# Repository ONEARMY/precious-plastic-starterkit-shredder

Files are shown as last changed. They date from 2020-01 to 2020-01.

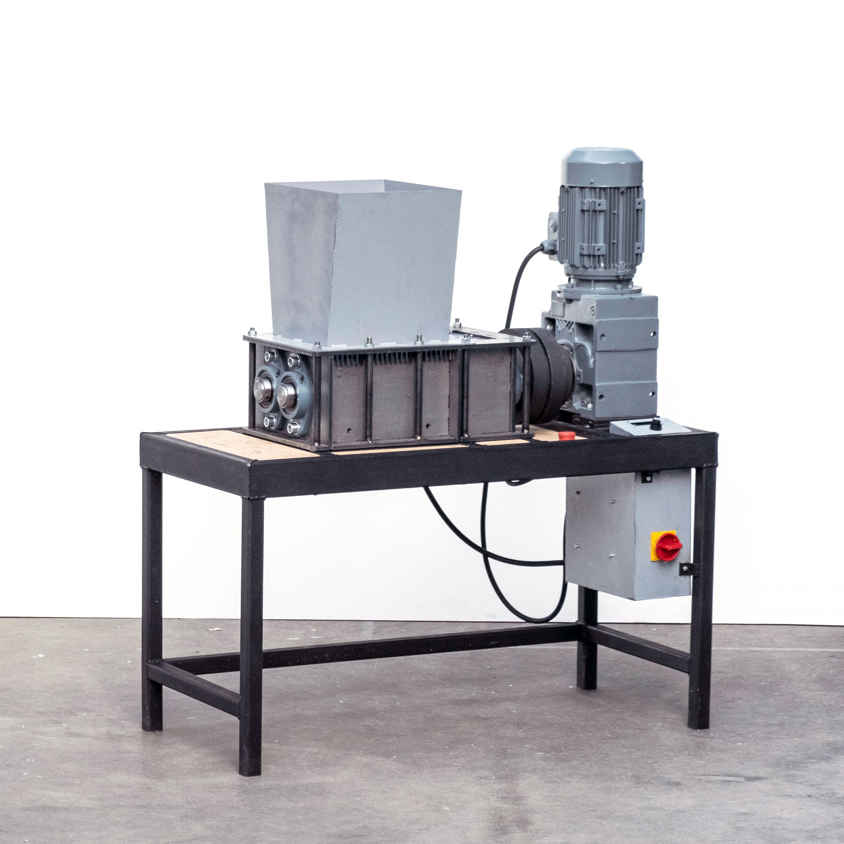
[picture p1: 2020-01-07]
3. Build the machine/Shredder-Pro-image.jpg

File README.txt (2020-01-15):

# Starterkit - Shredder Workspace V1.1

YEAH, you made it into a starter-kit!
Start with the 0. Start folder.. read the introduction text and make sure to watch the videos from our website.

If you have any questions visit our community platform or Discord
https://community.preciousplastic.com/
https://discordapp.com/invite/rnx7m4t

Good luck!!

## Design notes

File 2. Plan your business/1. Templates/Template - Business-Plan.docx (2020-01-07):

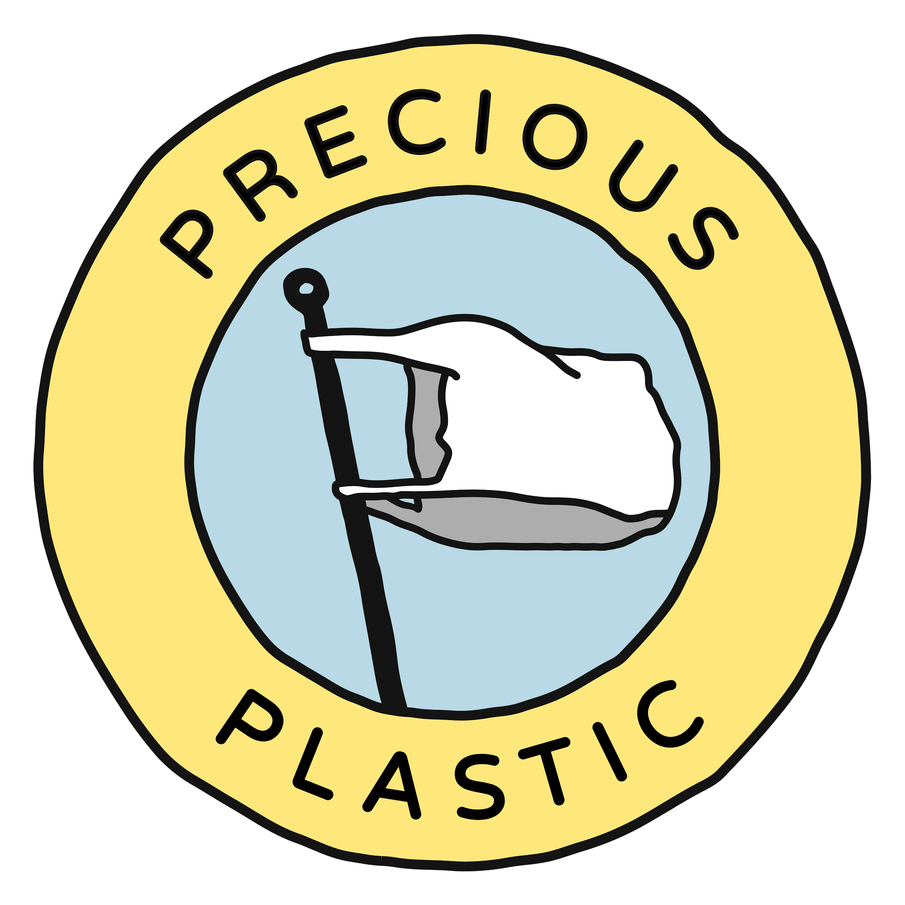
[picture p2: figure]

Your Logo and Business Name Here 👆

# Contact Details

Contact name:

Address:

City:

Zip:

Email:

Phone Number:

Website URL :

# Outline

1. Executive summary
2. Mission
3. Team
4. Market Analysis
  a. Product and Services
  b. Target Groups
  c. Engagement
  d. Sales Channels
5. Operations
  a. Key Resources
  b. Key Activities
  c. Running Costs
  d. Collaborators
6. Impact Measures
  a. Community
  b. Planet
  c. Income Streams
7. Financials
8. Legal Structure
9. Appendix

# 1. Executive Summary

This is your chance to quickly make your argument of what the problem is and how your business is going to solve it. This section shouldn’t be more than a couple paragraphs. Quickly cover the problem, your unique solution, who you’re targeting, and what your impact will be. It’s best to write this section after you’ve completed the whole business plan.

# 2. Mission

What’s the problem?

It’s best to start off describing what problem you’re solving. If your audience might need some education about the plastic waste problem - here’s your chance. What part or aspect of the plastic waste problem are you focusing on? You can set some context about the global plastic waste issue, but make sure to drill down to your national and local level as well. Try to be specific and stress why this is such a big problem facing the planet and your local community. Show your passion for solving this problem. This section will set the stage for the whole story told throughout the plan.

What’s your solution?

Next briefly cover how your solution addresses this problem. For example, if you write about how the plastic waste problem is due to a lifestyle issue, maybe you’re solution is focused on educating people because it addresses the root cause of the problem.

What’s your mission statement?

Look back on your mission that you filled out in the action plan. How can you elaborate to explain it to your reader?

What’s your vision?

Once you have explained your mission - write just a few sentences about your vision. What kind of world do you envision, and what do you envision for your organization?

# 3. Team

Fill in some basic information about your team to show who’s involved and what relevant skills and experience they have to the business.

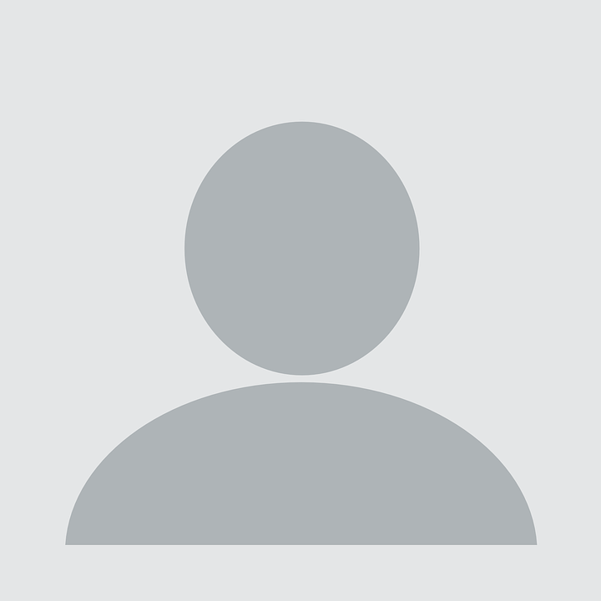
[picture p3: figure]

Name: Role: Experience: | Name: Role: Experience: | Name: Role: Experience:

# 4. Market Analysis

The market analysis section (broken down by the right side of the action plan), is where you will describe how the market is currently performing in your area of interest, how you plan to enter the market, what makes you different, who you are targeting, and how you will deliver your products and services to the customer.

## A. Products & Services

Product explanation

Explain that there is something missing from the market currently and what unique products or services you will offer to meet that unmet need. Write down a brief description of the products and services you are planning to make and include some pictures if possible. Include the price range they will be in and how this compares to similar products/services. If you have any sketches or pictures of your products, you can also include them here.

Product Photos or Sketches:

Competitive advantage

It’s unlikely that your product or service is completely unique - there are businesses or organizations that are probably doing something similar. What are those businesses, what are they offering, and how are you differentiating yourself? Another way to ask this what is your competitive advantage? What are you doing that sets you apart? Describe it here.

Total Available Market

What would you estimate to be the total available market for your product or service? For example, I’m targeting the plastic waste generated in my town, and I know from my city waste department that we generate about 100 tons per month of waste plastic. That means if we were to capture 100 % of the market, we would be processing all 100 tons. If we value each ton at $10, that a $12,000 total available market per year. You should include the total available market that you’re targeting to show how big your business could potentially grow.

## B. Target Groups

Identify the groups

In this section, explain who your target customer groups are, and how many potential customers are in this group. What do you know about these groups? This is your chance to communicate your research about your customers.

Research

What research have you done to show that your target groups will be interested in your products and services? Discuss any field research that you’ve done or online research about these groups. For example, if you’re producing craft furniture from plastic waste, do some research online to see if you can find numbers on the total craft furniture market value in your country. You could also run a small survey in your area to gauge interest in your products.

If you’re targeting businesses, do you have any letters of intent or proof that they are willing to buy your product or service when you’re able to get up and running? This can be a very powerful tool for showing your business case - you already have customers lining up to buy.

## C. Engagement

Engagement is how you will engage with your target customer groups and how many people you can potentially reach with this engagement strategy. What marketing channels are you using? If you’re using social media - which platforms? What’s your engagement rollout plan? Do you intend to start with one marketing channel and then gradually expand? Communicate your marketing plan here.

## D. Sales Channels

Finally, explain what your sales channels are. Explain where and how people can buy your products/services. Explain why you chose these sales channels, and relate that back to your target groups.

Business to Business (B to B) versus Business to Consumer (B to C)

Are you focusing on business to consumer or business to business? This is an important distinction, because it will help the reader understand your business model. Business to consumer (B to C) means that you are targeting consumers directly - you will be the one selling the product or service to the end user. If you are instead focusing on business to business (B to B), that means that you’ll be selling to other businesses. For example - if you’re a machine builder that will be selling machines to new workspaces - this is a business to business model. If you are a product producer selling products directly to people through the Precious Plastic Bazar, this is an example of business to consumer.

# 5. Operations

## A. Key Resources

First explain what key resources, or the key tools, machines, people, and any other resources that are crucial for you to deliver on your mission.

Another good thing to include here is any permits or licenses that you might need from the government in order to be able to operate. Are there any safety requirements that you need to follow? What resources do you need to have available in order to do so? What about people - are there any key skill sets that you need?

Include any pictures of your workspace if it’s relevant as well.

## B. Key Tasks

Explain your key tasks - What actions and activities will you need to focus on? Show that you have a clear sense of what needs to be done. How will produce your product or service and what are the key tasks that you must do to support this core delivery. Describe your production or service delivery process in detail and how you will maintain quality. How do you and your team’s skills and experience match up with these activities?

## C. Running Costs

In this section you will describe in more detail the key running costs that you identified in the Action Plan. Doesn’t need to be very long - this is just to show that you’ve thought about the costs that are a risk to the business month after month. If you have a way to control these costs, discuss that here as well.

## D. Collaborators

Finally, write about who your key collaborators are. What people, groups and organizations will be key in helping you fulfill your mission? Say what they will add to your business, and what your current relationship is with them. Are these people you would like to collaborate with, or you’ve already started? What’s the current status? How will they help you deliver on your mission? Be specific here - show what strategic relationships that you have which will be a strategic asset to your business.

# 6. Impacts

## A. Community

Here’s your chance to write about the positive impact you will have on your community. What’s the direct impact you will have on improving the lives of real people? Link this back to your mission and vision if possible.

You can also discuss your involvement with the Precious Plastic community. Perhaps discuss how you will contribute back to the Precious Plastic open source community and share your knowledge with other Precious Plastic workspaces.

## B. Planet

The planet section is for you to discuss the positive impact you will have on the environment. Show your vision and dream about a cleaner, greener future. It’s important to think about how you will measure this as well. For many Precious Plastic businesses this will be the amount of material recycled.

## C. Income Streams

Next describe your revenue model, or how you intend to bring in money month after month. Refer back to what you wrote in the action plan - is it product sales, workshop ticket sales, machine maintenance fees, or some other revenue model? How do you intend to price your products and services? Do you have different models for different products and services? Describe each one in detail.

# 7. Financials

The financials section is where you will build holistic financial picture to argue that you can turn your idea into a financially successful business.

First, write about the investment costs that you will have to pay in order to get started. You can pull this information from the workspace calculator and paste into a table. Copy in the investment costs table from the workspace calculator and add a total value.

Investment Costs
Initial Investments | Cost
Total:

Next describe how you intend to raise the initial money you need to get started. Is this a bank loan, grants, your private money, or assistance from the local government? Describe the different forms of financial assistance that you are pursuing.

Next you should copy in the Profit & Loss statement from the workspace calculator generated on the “extras” page. The profit and loss statement shows your estimated financial outlook for the first three years of operation.

Profit and Loss Statement
| Year 1 | Year 2 | Year 3
Revenue
Cost of Sales
Net Revenue
Fixed Costs
Gross Income from Operations
Business Taxes
Net Income

The cash flow statement shows that you will have enough money on hand to meet your financial obligations throughout the first year. Grants or bank loan applications often ask for these statements.

Cash Flow Statement
Month
Money In Bank (Beginning of Month)
Initial Investment
Revenue
Total Cash In
Investment Costs
Variable Costs
Fixed Costs
Total Cash Out
Net Cash Flow
Money In Bank (End of Month)

8. Legal Structure

The legal structure section is where to describe how you’ll be organized as a legal entity, or how you’re registered with the government. Your project doesn’t need to be structured as a commercial business - could be a non-profit, association, cooperative, project within an existing business, B - corp, social business. “Business plan” is the terminology that’s often used for a plan such as this, but doesn’t mean you need to run it necessarily as a “for-profit” business. This is going to depend on your situation, and could also depend on your country - sometimes it’s easier to structure a project a certain way depending on the legal entity regulations. One or the other maybe more tax friendly - more often a non-for profit or association is the more favorable tax structure for receiving grants. Describe here which legal structure you intend to use and why.

# 9. Appendix

The appendix is the place at the end of your business plan for any other supporting documents, pictures, graphs, or anything else you can think of that will help build your case. You can refer to items in the appendix throughout your document. Some items that could be found here are signed letters of intent from businesses wanting to buy your product, extra pictures of your products or services, additional financial graphs, and letters of understanding between you and collaborators.

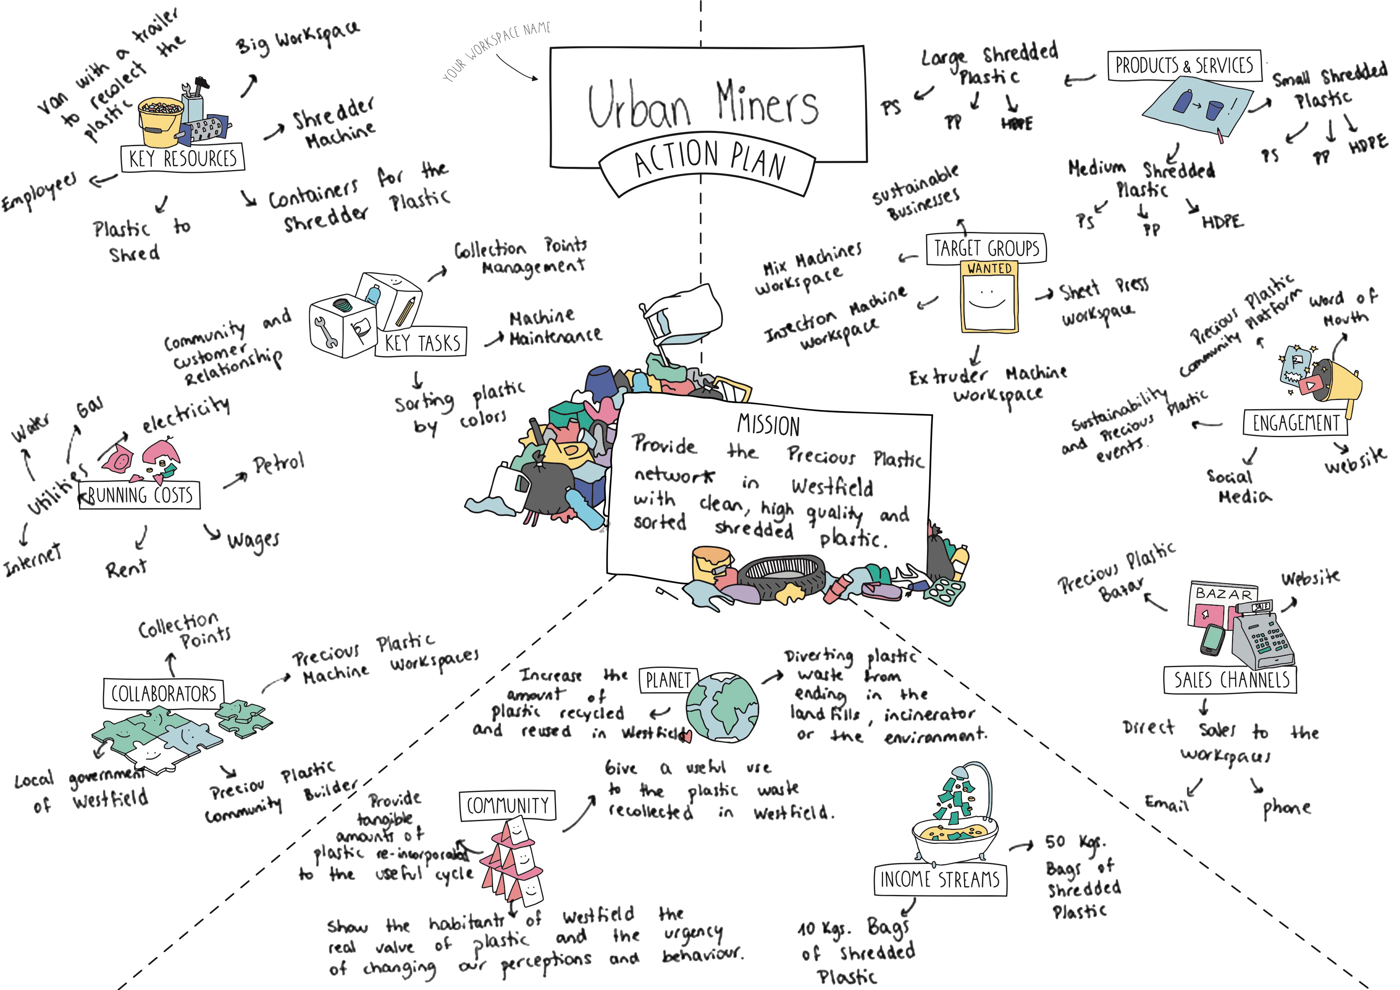
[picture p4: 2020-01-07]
2. Plan your business/2. Example (Shredder)/Urban Miners - Action Plan.png

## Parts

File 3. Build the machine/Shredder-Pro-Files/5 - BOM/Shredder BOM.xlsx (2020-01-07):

Type | Item | Qty. | URL (Europe) | Price | Part/Assembly Number | Notes
Service | gears keyway machining | 2 | https://www.gta.nl/ | €60.00 | SHRPRO-V1 1100.03-A, SHRPRO-V1 1100.04-A
Beams and Sheets | mild steel, OD19mm x ID16mm | 0,3m | https://www.danielsmetalen.nl/prijslijst_constructiestalen_plaatmaterialen.pdf#page=1 | €0.68 | SHRPRO-V1 1100.05-A
Beams and Sheets | mild steel, OD16mm x ID12mm | 2,1m | https://www.danielsmetalen.nl/prijslijst_constructiestalen_plaatmaterialen.pdf#page=1 | €3.81 | SHRPRO-V1 1110.13-A
Beams and Sheets | mild steel, Tube 40 x 40 x 3mm | 6m | https://www.danielsmetalen.nl/prijslijst_constructiestalen_plaatmaterialen.pdf#page=1 | €19.03 | SHRPRO-V1 1410.00-A
Beams and Sheets | mild steel, Tube 40 x 80 x 3mm | 6m | https://www.danielsmetalen.nl/prijslijst_constructiestalen_plaatmaterialen.pdf#page=1 | €32.61 | SHRPRO-V1 1410.00-A
Beams and Sheets | laser cut, V4 shredder mild steel & Hardox | ALL | https://www.247tailorsteel.com/en/cnc-laser-cutting | €830.00 | See DXF folder
Beams and Sheets | mild steel, 50mm Hex Bar C45 | 1,8m | https://www.acier-detail-decoupe.fr/aciers-doux/2783-acier-etire-mi-dur-a60c45.html | €132.30 | SHRPRO-V1 1120.13-A / SHRPRO-V1 1130.02-A
Fastners | DIN 912 M16 x 40 | 8 | https://shop.eriks.nl/en/fasteners-bolts-socket-head-cap-screws-fillister-head-screws/din912-hex-socket-head-cap-screw-steel-8-8-zinc-plated-m16x40mm-23241310/ | €6.48 | SHRPRO-V1 22
Fastners | DIN 912 M16 x 30 | 4 | https://shop.eriks.nl/en/fasteners-bolts-socket-head-cap-screws-fillister-head-screws/din912-hex-socket-head-cap-screw-steel-8-8-zinc-plated-m16x30mm-23241308/ | €2.64 | SHRPRO-V1 23
Fastners | M16 Washer | 12 | https://shop.eriks.nl/en/fasteners-washers-plain-washers/flat-washer-steel-electrolytic-zinc-plated-din-125-m16-23256098/ | €1.20 | SHRPRO-V1 24
Fastners | DIN 912 M5 x 12mm | 6 | https://shop.eriks.nl/en/fasteners-bolts-socket-head-cap-screws-fillister-head-screws/din912-hex-socket-head-cap-screw-steel-8-8-zinc-plated-m5x12mm-23241187/ | €0.24 | SHRPRO-V1 25
Fastners | M6 Washer | 4 | https://shop.eriks.nl/en/fasteners-washers-plain-washers/flat-washer-steel-electrolytic-zinc-plated-din-125-m6-23256090/ | €0.04 | SHRPRO-V1 26
Fastners | DIN 912 M6 x 12mm | 17 | https://shop.eriks.nl/en/fasteners-bolts-socket-head-cap-screws-fillister-head-screws/din912-hex-socket-head-cap-screw-steel-8-8-zinc-plated-m6x12mm-23241203/ | €0.85 | SHRPRO-V1 27
Fastners | M6 Nut | 13 | https://shop.eriks.nl/en/fasteners-nuts-hexagonal-full-nuts/hex-nut-din934-steel-10-9-m6-23238448/ | €0.13 | SHRPRO-V1 28
Fastners | M12 Threaded bar | 4 | https://shop.eriks.nl/en/fasteners-threaded-rods-and-ends-threaded-rods/din975-10-9-m12-1-threaded-rods-length-1m-23247427/ | €14.20 | SHRPRO-V1 1110.14-A, SHRPRO-V1 1110.15-A
Fastners | M12 Washer | 16 | https://shop.eriks.nl/en/fasteners-washers-plain-washers/flat-washer-steel-electrolytic-zinc-plated-din-125-m12-23256124/ | €0.64
Fastners | M12 Nut | 16 | https://shop.eriks.nl/en/fasteners-nuts-hexagonal-full-nuts/hex-nut-din934-steel-10-9-m12-23238451/ | €1.44 | SHRPRO-V1 29
Fastners | DIN 933 M10 x 40mm | 4 | https://shop.eriks.nl/en/fasteners-bolts-hexagonal-bolts-hexagon-set-screws/din933-10-10-9-m10x40-100-zeskanttapbout-volledige-draad-23238289/ | €0.72 | SHRPRO-V1 30
Fastners | M10 Nut | 4 | https://shop.eriks.nl/en/fasteners-nuts-hexagonal-full-nuts/hex-nut-din934-steel-10-9-m10-23238450/ | €0.24 | SHRPRO-V1 31
Fastners | Slotted round nut DIN 1804 M50X1,50 | 4 | https://shop.eriks.nl/en/fasteners-nuts-round-nuts/d1804w-5-slott-rnd-nt-mf-m50x1-50-5-23244943/ | €64.00 | SHRPRO-V1 01
Motor | 3 kW motor, with Bevelgear Type | 1 | https://www.yr.com.tr/gst/mdk/formK-a.aspx | €1300.00 | SHRPRO-V1 03
 | OR 2,2 kW motor, with Bevelgear Type | 1 | https://www.yr.com.tr/gst/mdk/formK-a.aspx | €920.00 | SHRPRO-V1 03
Electronics | full bridge rectifier 1A (DF10-G) | 1 | https://nl.rs-online.com/web/p/bridge-rectifiers/1699141/ | €0.19 | NA
Electronics | 100uF capacitor 10V | 1 | https://nl.rs-online.com/web/p/aluminium-capacitors/7076530/ | €0.42 | NA
Electronics | 10k resistors 1/4W | 2 | https://nl.rs-online.com/web/p/through-hole-fixed-resistors/1663958/ | €0.42 | NA
Electronics | 100k resistor 1/4W | 1 | https://nl.rs-online.com/web/p/through-hole-fixed-resistors/7077824/ | €0.16 | NA
Electronics | 2.2mF capacitor 10V | 1 | https://nl.rs-online.com/web/p/aluminium-capacitors/7110860/ | €0.36 | NA
Electronics | Arduino nano | 1 | https://store.arduino.cc/arduino-nano | €24.20 | SHRPRO-V1 10
Electronics | 5V 2 channels relay module 250VAC | 1 | https://www.ebay.com/itm/5V-Two-2-Channel-Relay-Module-With-optocoupler-For-PIC-AVR-DSP-ARM-Arduino/192724853675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 | €1.39 | SHRPRO-V1 11
Electronics | ACS712 30A hall effect sensor module | 1 | https://www.conrad.com/p/current-sensor-me067-iduino-me067-1616236 | €8.99 | SHRPRO-V1 12
Electronics | 3 position toggle switch | 1 | https://nl.rs-online.com/web/p/rotary-cam-switches/2579570/ | €38.99 | SHRPRO-V1 13
Electronics | 3 phase general switch | 1 | https://nl.rs-online.com/web/p/non-fused-switch-disconnectors/0466148/ | €20.05 | SHRPRO-V1 14
Electronics | Emergency stop switch with 3 NC connections | 1 | https://nl.rs-online.com/web/p/emergency-stop-push-buttons/8337032/ | €38.15 | SHRPRO-V1 15
Electronics | Motor protective circuit breaker, 6,8 Amps | 1 | https://nl.rs-online.com/web/p/motor-protection-circuit-breakers/7740146/ | €138.42 | SHRPRO-V1 16
Electronics | 3 phase contactors, 3 NO and 1 NC connections | 2 | https://nl.rs-online.com/web/p/contactors/3927835/ | €69.22 | SHRPRO-V1 17
Electronics | 5V 500mA power supply | 1 | https://nl.rs-online.com/web/p/din-rail-power-supplies/1368304/ | €24.73 | SHRPRO-V1 18
Electronics | Cable gland M25 | 4 | https://nl.rs-online.com/web/p/cable-glands/4442953/ | €9.92 | SHRPRO-V1 19
Electronics | DIN Rail Mount Terminal Block, 32 A | 10 | https://nl.rs-online.com/web/p/non-fused-terminal-blocks/7961160/ | €13.20 | SHRPRO-V1 20
Electronics | DIN Rail | 0.6 | https://nl.rs-online.com/web/p/din-rails/0467416/ | €7.03 | SHRPRO-V1 21
Electronics | 16A Male Plug | 1 | https://www.hornbach.nl/shop/PCE-CEE-Fase-inverter-16A/828911/artikel.html | €9.50 | NA
Electronics | H07 5 Multi-core Cable (6mm) | 1 | https://www.neopreen-kabel.nl/5-aderige-neopreenkabel/24-5-x-25-mm2-neopreenkabel-tm-99-meter.html | €24.20 | NA
Misc. | bearings, UCFL 209 45mm | 6 | https://www.conrad.nl/p/flenslager-htb-gietijzer-ucfl-208-boordiameter-40-mm-gatafstand-144-mm-197075 | €182.16 | SHRPRO-V1 02
Misc. | Coupling FENNERHRC Elastomeric - hub size 230 - type F with tapered bore for Taper Lock 3020 | 2 | https://shop.eriks.nl/en/hrc-elastomeric-coupling-hub-size-230-type-f-with-tapered-bore-for-taper-lock-3020-11423343/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 | €239.84 | SHRPRO-V1 06
Misc. | FENNER Spider for HRC jaw coupling size 230 | 1 | https://shop.eriks.nl/en/spider-for-hrc-jaw-coupling-size-230-11423345/ | €54.26 | SHRPRO-V1 07
Misc. | Taper Lock 3020-45 | 1 | https://shop.eriks.nl/en/mechanical-power-transmission-shaft-fixings-conical-clamping-bushes-taper-bush-taper-lock-bushes-metric-bore/taper-lock-bush-metric-b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 | €25.96 | SHRPRO-V1 08
Misc. | Taper Lock 3020-50 | 1 | https://shop.eriks.nl/en/mechanical-power-transmission-shaft-fixings-conical-clamping-bushes-taper-bush-taper-lock-bushes-metric-bore/taper-lock-bush-metric-b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 | €25.96 | SHRPRO-V1 09
Misc. | Spur Gears, Steel C45, Hardened Teeth, Module 6 18 teeth | 1 | https://www.maedler.de/product/1643/1618/1034/2314/stirnzahnraeder-aus-stahl-c45-verzahnung-gehaertet-modul-6 | €108.90 | SHRPRO-V1 1100.03-A
Misc. | Spur Gears, Steel C45, Hardened Teeth, Module 6 20 teeth | 1 | https://www.maedler.de/product/1643/1618/1034/2314/stirnzahnraeder-aus-stahl-c45-verzahnung-gehaertet-modul-6 | €108.90 | SHRPRO-V1 1100.04-A
Misc. | Parallel key A14 x 9 x 70 DIN 6885 | 2 | https://www.fabory.com/nl/vlakke-inlegspie-met-ronde-einden-hoog-type-din-6885-a-staal-c45%2bc-blank-14x9x70mm/p/39250149070 | €2.00 | SHRPRO-V1 04
Misc. | Parallel key A14 x 9 x 80 DIN 6885 | 1 | https://www.fabory.com/nl/vlakke-inlegspie-met-ronde-einden-hoog-type-din-6885-a-staal-c45%2bc-blank-14x9x80mm/p/39250149080 | €1.00 | SHRPRO-V1 05
 |  |  | Total without motor : | €2349.769883
 |  |  | Total with 3kW motor : | €3649.769883
 |  |  | Total with 2,2kW motor : | €3269.769883

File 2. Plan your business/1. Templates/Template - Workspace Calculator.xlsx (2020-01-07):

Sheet: Read Me!
Precious Plastic Workspace Calculator
 | Welcome to the Precious Plastic Workspace Calculator! This tool will help you understand the numbers behind starting a Precious Plastic business.
You will learn:
- How much money you need to start your workspace
- How long it will take to pay back your intitial investment
- What prices for your products will cover the costs of production
Before you get started:
1. Only fill in cells that are bordered in blue
2. Get started by clicking on the sales tab below
 |  | Cells where you should enter numbers
 |  | Cells with numbers we calculate for you
 |  | If you click cells with red arrows, more information pops up

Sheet: 1. Sales
Sales
In the first column, list all the products, machines, workshops or services that you plan on selling with your Precious Plastic workspace. In the second column, estimate how much each product or service would cost you in materials. In the third column, estimate the time it will take to create each product or service.
Products or Services | Material Cost for Each Product | Number of Working Hours to Produce Each Product or Service

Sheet: 2. Costs
Working Hours |  | Investment Costs |  | Fixed Costs
Besides making products & services, you will have to spend time on doing other tasks. In this section, fill in your weekly activities and how many hours you will spend on each activity per week. Do not include the time to directly produce products or services. |  | These are the machines, tools, and other expenses you need to set up your workspace. These costs are also known as your "investment costs" and are only paid once. |  | Fixed costs are the costs that do not vary with the amount of products and services that you produce, but you have to pay on a regular basis. Some costs may need to be paid quarterly or yearly, so do some quick calculations to estimate them on a monthly basis.
Weekly Activities | Hours per Week | Initial Investments | Cost | Fixed Costs | Cost per Month

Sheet: 3. Dashboard
Dashboard | Sales Overview |  |  |  |  | Wages
 | Products & Services | Selling Price Per Unit | Number of Expected Sales Per Month | Total Product Cost | Profit Margin | Hourly Wage
Start by entering your desired hourly wage, selling prices, and expected sales for each product. Then play around with your pricing, hourly wage, and expected sales to see how it affects the time needed to pay back your investment, monthly profit, and monthly pay. Make sure you set prices for your products and services so that the numbers in the profit margin column turn green, which means you are covering the costs of producing them. |  |  |  |  |  |  | 3 | *
 |  |  |  |  |  | Summary
 |  |  |  |  |  | Money Needed to Start
 |  |  |  |  |  | Months to Pay Back Investment | Too Long!
 |  |  |  |  |  | Full Time Employees Needed | 0.0
 |  |  |  |  |  | Revenue Earned Per Month | 0.00
 |  |  |  |  |  | Fixed Costs Per Month | 0.00
 |  |  |  |  |  | Material Costs Per Month | 0.00
 |  |  |  |  |  | Total Wages Paid Per Month | 0.00
 |  |  |  |  |  | Total Profit Earned Per Month | 0

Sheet: Extras
Extras
This page provides you with some basic finanial statements (Cashflow and Profit & Loss) and shows you the calculations from the previous pages. It's more for those people who want to dive deep into the numbers or provide a bank with forecasted financial statements.
Cash Flow A cash flow analysis shows that you have enough money throughout your first year to buy materials, pay your employees, or make an investment into a new machine.
 | Month 1 | Month 2 | Month 3 | Month 4 | Month 5 | Month 6 | Month 7 | Month 8 | Month 9 | Month 10 | Month 11 | Month 12
Money In Bank (Beginning of Month) |  | 0.00 | 0.00 | 0.00 | 0.00 | 0.00 | 0.00 | 0.00 | 0.00 | 0.00 | 0.00 | 0.00
Initial Investment
Revenue | 0.00 | 0.00 | 0.00 | 0.00 | 0.00 | 0.00 | 0.00 | 0.00 | 0.00 | 0.00 | 0.00 | 0.00
Total Cash In | 0.00 | 0.00 | 0.00 | 0.00 | 0.00 | 0.00 | 0.00 | 0.00 | 0.00 | 0.00 | 0.00 | 0.00
Investment Costs | 0.00
Variable Costs | 0.00 | 0.00 | 0.00 | 0.00 | 0.00 | 0.00 | 0.00 | 0.00 | 0.00 | 0.00 | 0.00 | 0.00
Fixed Costs | 0.00 | 0.00 | 0.00 | 0.00 | 0.00 | 0.00 | 0.00 | 0.00 | 0.00 | 0.00 | 0.00 | 0.00
Total Cash Out | 0.00 | 0.00 | 0.00 | 0.00 | 0.00 | 0.00 | 0.00 | 0.00 | 0.00 | 0.00 | 0.00 | 0.00
Net Cashflow | 0.00 | 0.00 | 0.00 | 0.00 | 0.00 | 0.00 | 0.00 | 0.00 | 0.00 | 0.00 | 0.00 | 0.00
Money In Bank (End of Month) | 0.00 | 0.00 | 0.00 | 0.00 | 0.00 | 0.00 | 0.00 | 0.00 | 0.00 | 0.00 | 0.00 | 0.00
Profit and Loss This table is to show how much money the company is projected to make each year. It assumes that you paid yourself for the hours you worked, so the "Net Income" at the bottom is the remaining profit made by your company. It is greatly influenced by the "Monthly Sales Improvement Rate" on the Dashboard page. This table is also useful to show your bank or include in grant applications.
 | Year 1 | Year 2 | Year 3 |  | Yearly Growth Rate
Revenue | 0.00 | 0.00 | 0.00 |  | Low
Cost of Sales | 0.00 | 0.00 | 0.00 |  | 0.10 €
Net Revenue | 0.00 | 0.00 | 0.00
Fixed Costs | 0.00 | 0.00 | 0.00
Gross Income from Operations | 0.00 | 0.00 | 0.00
 |  |  |  |  | Business Tax Rate (Research for your Country)
Business Taxes | 0.00 | 0.00 | 0.00 |  | 20.00%
Net Income | 0.00 | 0.00 | 0.00
Monthly Sales Figures
Products and Services | Revenue | Overhead Cost | Indirect Labor Cost | Production Labor Cost | Material Cost | Total Monthly Cost | Total Monthly Profit | Total Monthly Hours
 |  |  |  |  |  |  | #VALUE! | 0.00
 |  | #DIV/0! | #DIV/0! |  |  | #DIV/0!
 |  |  |  |  |  |  | #VALUE! | 0.00
 |  | #DIV/0! | #DIV/0! |  |  | #DIV/0!
 |  |  |  |  |  |  | #VALUE! | 0.00
 |  | #DIV/0! | #DIV/0! |  |  | #DIV/0!
 |  |  |  |  |  |  | #VALUE! | 0.00
 |  | #DIV/0! | #DIV/0! |  |  | #DIV/0!
 |  |  |  |  |  |  | #VALUE! | 0.00
 |  | #DIV/0! | #DIV/0! |  |  | #DIV/0!
 |  |  |  |  |  |  | #VALUE! | 0.00
 |  | #DIV/0! | #DIV/0! |  |  | #DIV/0!
 |  |  |  |  |  |  | #VALUE! | 0.00
 |  | #DIV/0! | #DIV/0! |  |  | #DIV/0!
 |  |  |  |  |  |  | #VALUE! | 0.00
 |  | #DIV/0! | #DIV/0! |  |  | #DIV/0!
 |  |  |  |  |  |  | #VALUE! | 0.00
 |  | #DIV/0! | #DIV/0! |  |  | #DIV/0!
 |  |  |  |  |  |  | #VALUE! | 0.00
 |  | #DIV/0! | #DIV/0! |  |  | #DIV/0!
 |  |  |  |  |  |  | #VALUE! | 0.00
 |  | #DIV/0! | #DIV/0! |  |  | #DIV/0!
Total Revenue | 0.00 |  |  |  |  |  | #VALUE!
Total Cost |  | #DIV/0! | #DIV/0! | 0.00 | 0.00 | #DIV/0! |  | 0.00
Payback Table
Don't worry too much about this one, it's just to make the payback analysis graph on the dashboard | #DIV/0! | #DIV/0! | #DIV/0! | #DIV/0! | #DIV/0! | #DIV/0! | #DIV/0! | #DIV/0! | #DIV/0! | #DIV/0! | #DIV/0! | #DIV/0! | #DIV/0! | #DIV/0! | #DIV/0! | #DIV/0! | #DIV/0! | #DIV/0! | #DIV/0! | #DIV/0! | #DIV/0! | #DIV/0! | #DIV/0! | #DIV/0! | #DIV/0! | #DIV/0! | #DIV/0! | #DIV/0! | #DIV/0! | #DIV/0! | #DIV/0! | #DIV/0! | #DIV/0! | #DIV/0! | #DIV/0! | #DIV/0!
Month | 1 | 2 | 3 | 4 | 5 | 6 | 7 | 8 | 9 | 10 | 11 | 12 | 13 | 14 | 15 | 16 | 17 | 18 | 19 | 20 | 21 | 22 | 23 | 24 | 25 | 26 | 27 | 28 | 29 | 30 | 31 | 32 | 33 | 34 | 35 | 36
Money You Invested | #DIV/0! | #DIV/0! | #DIV/0! | #DIV/0! | #DIV/0! | #DIV/0! | #DIV/0! | #DIV/0! | #DIV/0! | #DIV/0! | #DIV/0! | #DIV/0! | #DIV/0! | #DIV/0! | #DIV/0! | #DIV/0! | #DIV/0! | #DIV/0! | #DIV/0! | #DIV/0! | #DIV/0! | #DIV/0! | #DIV/0! | #DIV/0! | #DIV/0! | #DIV/0! | #DIV/0! | #DIV/0! | #DIV/0! | #DIV/0! | #DIV/0! | #DIV/0! | #DIV/0! | #DIV/0! | #DIV/0! | #DIV/0!
Money You Invested (+) | #DIV/0! | #DIV/0! | #DIV/0! | #DIV/0! | #DIV/0! | #DIV/0! | #DIV/0! | #DIV/0! | #DIV/0! | #DIV/0! | #DIV/0! | #DIV/0! | #DIV/0! | #DIV/0! | #DIV/0! | #DIV/0! | #DIV/0! | #DIV/0! | #DIV/0! | #DIV/0! | #DIV/0! | #DIV/0! | #DIV/0! | #DIV/0! | #DIV/0! | #DIV/0! | #DIV/0! | #DIV/0! | #DIV/0! | #DIV/0! | #DIV/0! | #DIV/0! | #DIV/0! | #DIV/0! | #DIV/0! | #DIV/0!
Money You Invested (-) | #DIV/0! | #DIV/0! | #DIV/0! | #DIV/0! | #DIV/0! | #DIV/0! | #DIV/0! | #DIV/0! | #DIV/0! | #DIV/0! | #DIV/0! | #DIV/0! | #DIV/0! | #DIV/0! | #DIV/0! | #DIV/0! | #DIV/0! | #DIV/0! | #DIV/0! | #DIV/0! | #DIV/0! | #DIV/0! | #DIV/0! | #DIV/0! | #DIV/0! | #DIV/0! | #DIV/0! | #DIV/0! | #DIV/0! | #DIV/0! | #DIV/0! | #DIV/0! | #DIV/0! | #DIV/0! | #DIV/0! | #DIV/0!
Revenue | 0.00 | 0.00 | 0.00 | 0.00 | 0.00 | 0.00 | 0.00 | 0.00 | 0.00 | 0.00 | 0.00 | 0.00 | 0.00 | 0.00 | 0.00 | 0.00 | 0.00 | 0.00 | 0.00 | 0.00 | 0.00 | 0.00 | 0.00 | 0.00 | 0.00 | 0.00 | 0.00 | 0.00 | 0.00 | 0.00 | 0.00 | 0.00 | 0.00 | 0.00 | 0.00 | 0.00
Variable Cost | 0.00 | 0.00 | 0.00 | 0.00 | 0.00 | 0.00 | 0.00 | 0.00 | 0.00 | 0.00 | 0.00 | 0.00 | 0.00 | 0.00 | 0.00 | 0.00 | 0.00 | 0.00 | 0.00 | 0.00 | 0.00 | 0.00 | 0.00 | 0.00 | 0.00 | 0.00 | 0.00 | 0.00 | 0.00 | 0.00 | 0.00 | 0.00 | 0.00 | 0.00 | 0.00 | 0.00
Fixed Cost | #DIV/0! | #DIV/0! | #DIV/0! | #DIV/0! | #DIV/0! | #DIV/0! | #DIV/0! | #DIV/0! | #DIV/0! | #DIV/0! | #DIV/0! | #DIV/0! | #DIV/0! | #DIV/0! | #DIV/0! | #DIV/0! | #DIV/0! | #DIV/0! | #DIV/0! | #DIV/0! | #DIV/0! | #DIV/0! | #DIV/0! | #DIV/0! | #DIV/0! | #DIV/0! | #DIV/0! | #DIV/0! | #DIV/0! | #DIV/0! | #DIV/0! | #DIV/0! | #DIV/0! | #DIV/0! | #DIV/0! | #DIV/0!
Net Profit | #DIV/0! | #DIV/0! | #DIV/0! | #DIV/0! | #DIV/0! | #DIV/0! | #DIV/0! | #DIV/0! | #DIV/0! | #DIV/0! | #DIV/0! | #DIV/0! | #DIV/0! | #DIV/0! | #DIV/0! | #DIV/0! | #DIV/0! | #DIV/0! | #DIV/0! | #DIV/0! | #DIV/0! | #DIV/0! | #DIV/0! | #DIV/0! | #DIV/0! | #DIV/0! | #DIV/0! | #DIV/0! | #DIV/0! | #DIV/0! | #DIV/0! | #DIV/0! | #DIV/0! | #DIV/0! | #DIV/0! | #DIV/0!

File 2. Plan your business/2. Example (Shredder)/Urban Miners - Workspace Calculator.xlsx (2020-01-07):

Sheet: Read Me!
Precious Plastic Workspace Calculator
 | Welcome to the Precious Plastic Workspace Calculator! This tool will help you understand the numbers behind starting a Precious Plastic business.
You will learn:
- How much money you need to start your workspace
- How long it will take to pay back your intitial investment
- What prices for your products will cover the costs of production
Before you get started:
1. Only fill in cells that are bordered in blue
2. Get started by clicking on the sales tab below
 |  | Cells where you should enter numbers
 |  | Cells with numbers we calculate for you
 |  | If you click cells with red arrows, more information pops up

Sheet: 1. Sales
Sales
In the first column, list all the products, machines, workshops or services that you plan on selling with your Precious Plastic workspace. In the second column, estimate how much each product or service would cost you in materials. In the third column, estimate the time it will take to create each product or service.
Products or Services | Material Cost for Each Product | Number of Working Hours to Produce Each Product or Service
10 kgs of Large Shredded Plastic | 0.00 | 0.16
10 kgs of Medium Shredded Plastic | 0.00 | 0.33
10 kgs of Small Shredded Plastic | 0.00 | 0.50
50 kgs of Large Shredded Plastic | 0.00 | 0.80
50 kgs of Medium Shredded Plastic | 0.00 | 1.65
50 kgs of Small Shredded Plastic | 0.00 | 2.50

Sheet: 2. Costs
Working Hours |  | Investment Costs |  | Fixed Costs
Besides making products & services, you will have to spend time on doing other tasks. In this section, fill in your weekly activities and how many hours you will spend on each activity per week. Do not include the time to directly produce products or services. |  | These are the machines, tools, and other expenses you need to set up your workspace. These costs are also known as your "investment costs" and are only paid once. |  | Fixed costs are the costs that do not vary with the amount of products and services that you produce, but you have to pay on a regular basis. Some costs may need to be paid quarterly or yearly, so do some quick calculations to estimate them on a monthly basis.
Weekly Activities | Hours per Week | Initial Investments | Cost | Fixed Costs | Cost per Month
Managing collection points and drop off sites | 25.0 | Shredder Pro | 5300.00 | Rent | 300.00
Extra sorting by colours and washing | 25.0 | Workspace Renovation | 800.00 | Water | 70.00
Marketing/Social Media/Website | 6.0 | Business license and permits | 300.00 | Electricity | 60.00
Administation | 7.0 | Van | 3000.00 | Gas | 30.00
Machine/Workspace Maintenance | 8.0 | Washing/Sorting setup | 500.00 | Internet | 30.00
Sales | 9.0 | Coffee Machine | 20.00 | Insurance | 70.00
 |  | First Aid Kit | 45.00 | Office Snacks | 80.00
 |  | Office Supplies | 120.00 | Car Insurance/Maintenance | 120.00
 |  | Computer | 300.00 | Website Service | 10.00
 |  | Speaker | 25.00 | Office Supplies | 20.00
 |  | Trailer for the Van | 300.00 | Machine maintenance kit | 50.00
 |  | Storage bags | 8.00 | Safety Kit (mascarillas) | 15.00
 |  | Storage bag hangers | 4.00
 |  | Sorting container | 15.00
 |  | Shredded plastic containers | 15.00
 |  | Shredded plastic storage shelf | 15.00
 |  | Workbench | 25.00
 |  | Shredding trolley | 10.00
 |  | Cleaning brush | 2.00
 |  | Rubber mallet | 12.00
 |  | Wrenches | 25.00
 |  | Allen keys | 5.00
 |  | Scale | 20.00

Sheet: 3. Dashboard
Dashboard | Sales Overview |  |  |  |  | Wages
 | Products & Services | Selling Price Per Unit | Number of Expected Sales Per Month | Total Product Cost | Profit Margin | Hourly Wage | 10.00
Start by entering your desired hourly wage, selling prices, and expected sales for each product. Then play around with your pricing, hourly wage, and expected sales to see how it affects the time needed to pay back your investment, monthly profit, and monthly pay. Make sure you set prices for your products and services so that the numbers in the profit margin column turn green, which means you are covering the costs of producing them. | 10 kgs of Large Shredded Plastic | 12.00 | 50.0 | 8.90 | 34.82% |  | 3 | *
 | 10 kgs of Medium Shredded Plastic | 25.00 | 30.0 | 18.36 | 36.18%
 | 10 kgs of Small Shredded Plastic | 35.00 | 20.0 | 27.82 | 25.83% | Summary
 | 50 kgs of Large Shredded Plastic | 48.00 | 15.0 | 44.51 | 7.85% | Money Needed to Start | 16131.50
 | 50 kgs of Medium Shredded Plastic | 100.00 | 15.0 | 91.79 | 8.94% | Months to Pay Back Investment | 25
 | 50 kgs of Small Shredded Plastic | 140.00 | 12.0 | 139.08 | 0.66% | Full Time Employees Needed | 2.6
 |  |  |  |  |  | Revenue Earned Per Month | 5950.00
 |  |  |  |  |  | Fixed Costs Per Month | 855.00
 |  |  |  |  |  | Material Costs Per Month | 0.00
 |  |  |  |  |  | Total Wages Paid Per Month | 4410.50
 |  |  |  |  |  | Total Profit Earned Per Month | 684.50

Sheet: Extras
Extras
This page provides you with some basic finanial statements (Cashflow and Profit & Loss) and shows you the calculations from the previous pages. It's more for those people who want to dive deep into the numbers or provide a bank with forecasted financial statements.
Cash Flow A cash flow analysis shows that you have enough money throughout your first year to buy materials, pay your employees, or make an investment into a new machine.
 | Month 1 | Month 2 | Month 3 | Month 4 | Month 5 | Month 6 | Month 7 | Month 8 | Month 9 | Month 10 | Month 11 | Month 12
Money In Bank (Beginning of Month) | 16131.50 | 9414.00 | 13562.50 | 17711.00 | 21859.50 | 26008.00 | 30156.50 | 34305.00 | 38453.50 | 42602.00 | 46750.50 | 50899.00
Initial Investment | 16131.50
Revenue | 5950.00 | 5950.00 | 5950.00 | 5950.00 | 5950.00 | 5950.00 | 5950.00 | 5950.00 | 5950.00 | 5950.00 | 5950.00 | 5950.00
Total Cash In | 22081.50 | 5950.00 | 5950.00 | 5950.00 | 5950.00 | 5950.00 | 5950.00 | 5950.00 | 5950.00 | 5950.00 | 5950.00 | 5950.00
Investment Costs | -10866.00
Variable Costs | -946.50 | -946.50 | -946.50 | -946.50 | -946.50 | -946.50 | -946.50 | -946.50 | -946.50 | -946.50 | -946.50 | -946.50
Fixed Costs | -855.00 | -855.00 | -855.00 | -855.00 | -855.00 | -855.00 | -855.00 | -855.00 | -855.00 | -855.00 | -855.00 | -855.00
Total Cash Out | -12667.50 | -1801.50 | -1801.50 | -1801.50 | -1801.50 | -1801.50 | -1801.50 | -1801.50 | -1801.50 | -1801.50 | -1801.50 | -1801.50
Net Cashflow | 9414.00 | 4148.50 | 4148.50 | 4148.50 | 4148.50 | 4148.50 | 4148.50 | 4148.50 | 4148.50 | 4148.50 | 4148.50 | 4148.50
Money In Bank (End of Month) | 9414.00 | 13562.50 | 17711.00 | 21859.50 | 26008.00 | 30156.50 | 34305.00 | 38453.50 | 42602.00 | 46750.50 | 50899.00 | 55047.50
Profit and Loss This table is to show how much money the company is projected to make each year. It assumes that you paid yourself for the hours you worked, so the "Net Income" at the bottom is the remaining profit made by your company. It is greatly influenced by the "Monthly Sales Improvement Rate" on the Dashboard page. This table is also useful to show your bank or include in grant applications.
 | Year 1 | Year 2 | Year 3 |  | Yearly Growth Rate
Revenue | 71400.00 | 78540.00 | 86394.00 |  | Low
Cost of Sales | 11358.00 | 12493.80 | 13743.18 |  | 0.10 €
Net Revenue | 60042.00 | 66046.20 | 72650.82
Fixed Costs | 10260.00 | 10260.00 | 10260.00
Gross Income from Operations | 49782.00 | 55786.20 | 62390.82
 |  |  |  |  | Business Tax Rate (Research for your Country)
Business Taxes | 9956.40 | 11157.24 | 12478.16 |  | 20.00%
Net Income | 39825.60 | 44628.96 | 49912.66
Monthly Sales Figures
Products and Services | Revenue | Overhead Cost | Indirect Labor Cost | Production Labor Cost | Material Cost | Total Monthly Cost | Total Monthly Profit | Total Monthly Hours
10 kgs of Large Shredded Plastic | 600.00 |  |  |  |  |  | 154.95 | 8.00
 |  | 72.27 | 292.78 | 80.00 |  | 445.05
10 kgs of Medium Shredded Plastic | 750.00 |  |  |  |  |  | 199.25 | 9.90
 |  | 89.43 | 362.32 | 99.00 |  | 550.75
10 kgs of Small Shredded Plastic | 700.00 |  |  |  |  |  | 143.69 | 10.00
 |  | 90.33 | 365.98 | 100.00 |  | 556.31
50 kgs of Large Shredded Plastic | 720.00 |  |  |  |  |  | 52.42 | 12.00
 |  | 108.40 | 439.18 | 120.00 |  | 667.58
50 kgs of Medium Shredded Plastic | 1500.00 |  |  |  |  |  | 123.13 | 24.75
 |  | 223.57 | 905.80 | 247.50 |  | 1376.87
50 kgs of Small Shredded Plastic | 1680.00 |  |  |  |  |  | 11.06 | 30.00
 |  | 271.00 | 1097.94 | 300.00 |  | 1668.94
Total Revenue | 5950.00 |  |  |  |  |  | #VALUE!
Total Cost |  | 855.00 | 3464.00 | 946.50 | 0.00 | 5265.50 |  | 94.65
Payback Table
Don't worry too much about this one, it's just to make the payback analysis graph on the dashboard | 0 | 0 | 0 | 0 | 0 | 0 | 0 | 0 | 0 | 0 | 0 | 0 | 0 | 0 | 0 | 0 | 0 | 0 | 0 | 0 | 0 | 0 | 0 | 0 | 1 | 1 | 1 | 1 | 1 | 1 | 1 | 1 | 1 | 1 | 1 | 1
Month | 1 | 2 | 3 | 4 | 5 | 6 | 7 | 8 | 9 | 10 | 11 | 12 | 13 | 14 | 15 | 16 | 17 | 18 | 19 | 20 | 21 | 22 | 23 | 24 | 25 | 26 | 27 | 28 | 29 | 30 | 31 | 32 | 33 | 34 | 35 | 36
Money You Invested | -16131.50 | -15447.00 | -14762.50 | -14078.00 | -13393.50 | -12709.00 | -12024.50 | -11340.00 | -10655.50 | -9971.00 | -9286.50 | -8602.00 | -7917.50 | -7233.00 | -6548.50 | -5864.00 | -5179.50 | -4495.00 | -3810.50 | -3126.00 | -2441.50 | -1757.00 | -1072.50 | -388.00 | 296.50 | 981.00 | 1665.50 | 2350.00 | 3034.50 | 3719.00 | 4403.50 | 5088.00 | 5772.50 | 6457.00 | 7141.50 | 7826.00
Money You Invested (+) | 0.00 | 0.00 | 0.00 | 0.00 | 0.00 | 0.00 | 0.00 | 0.00 | 0.00 | 0.00 | 0.00 | 0.00 | 0.00 | 0.00 | 0.00 | 0.00 | 0.00 | 0.00 | 0.00 | 0.00 | 0.00 | 0.00 | 0.00 | 0.00 | 296.50 | 981.00 | 1665.50 | 2350.00 | 3034.50 | 3719.00 | 4403.50 | 5088.00 | 5772.50 | 6457.00 | 7141.50 | 7826.00
Money You Invested (-) | -16131.50 | -15447.00 | -14762.50 | -14078.00 | -13393.50 | -12709.00 | -12024.50 | -11340.00 | -10655.50 | -9971.00 | -9286.50 | -8602.00 | -7917.50 | -7233.00 | -6548.50 | -5864.00 | -5179.50 | -4495.00 | -3810.50 | -3126.00 | -2441.50 | -1757.00 | -1072.50 | -388.00 | 0.00 | 0.00 | 0.00 | 0.00 | 0.00 | 0.00 | 0.00 | 0.00 | 0.00 | 0.00 | 0.00 | 0.00
Revenue | 5950.00 | 5950.00 | 5950.00 | 5950.00 | 5950.00 | 5950.00 | 5950.00 | 5950.00 | 5950.00 | 5950.00 | 5950.00 | 5950.00 | 5950.00 | 5950.00 | 5950.00 | 5950.00 | 5950.00 | 5950.00 | 5950.00 | 5950.00 | 5950.00 | 5950.00 | 5950.00 | 5950.00 | 5950.00 | 5950.00 | 5950.00 | 5950.00 | 5950.00 | 5950.00 | 5950.00 | 5950.00 | 5950.00 | 5950.00 | 5950.00 | 5950.00
Variable Cost | 946.50 | 946.50 | 946.50 | 946.50 | 946.50 | 946.50 | 946.50 | 946.50 | 946.50 | 946.50 | 946.50 | 946.50 | 946.50 | 946.50 | 946.50 | 946.50 | 946.50 | 946.50 | 946.50 | 946.50 | 946.50 | 946.50 | 946.50 | 946.50 | 946.50 | 946.50 | 946.50 | 946.50 | 946.50 | 946.50 | 946.50 | 946.50 | 946.50 | 946.50 | 946.50 | 946.50
Fixed Cost | 4319.00 | 4319.00 | 4319.00 | 4319.00 | 4319.00 | 4319.00 | 4319.00 | 4319.00 | 4319.00 | 4319.00 | 4319.00 | 4319.00 | 4319.00 | 4319.00 | 4319.00 | 4319.00 | 4319.00 | 4319.00 | 4319.00 | 4319.00 | 4319.00 | 4319.00 | 4319.00 | 4319.00 | 4319.00 | 4319.00 | 4319.00 | 4319.00 | 4319.00 | 4319.00 | 4319.00 | 4319.00 | 4319.00 | 4319.00 | 4319.00 | 4319.00
Net Profit | 684.50 | 684.50 | 684.50 | 684.50 | 684.50 | 684.50 | 684.50 | 684.50 | 684.50 | 684.50 | 684.50 | 684.50 | 684.50 | 684.50 | 684.50 | 684.50 | 684.50 | 684.50 | 684.50 | 684.50 | 684.50 | 684.50 | 684.50 | 684.50 | 684.50 | 684.50 | 684.50 | 684.50 | 684.50 | 684.50 | 684.50 | 684.50 | 684.50 | 684.50 | 684.50 | 684.50

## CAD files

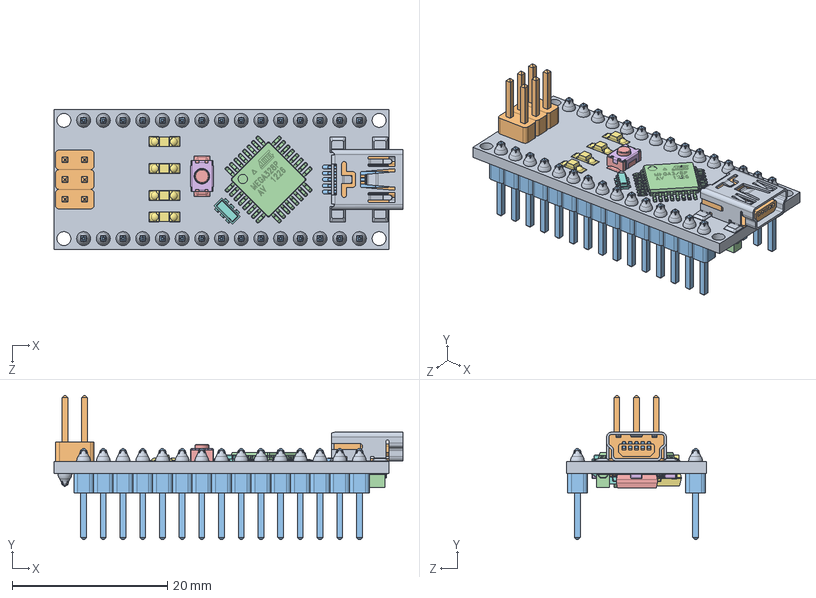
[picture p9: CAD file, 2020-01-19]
3. Build the machine/Shredder-Pro-Files/1 - 3D CAD/Shredder Solidworks CAD/00 - Commercial parts/Electronics/Arduino Nano/SHRPRO-V1 10 Arduino Nano.SLDASM
45.0 x 18.6 x 18.0 mm
nano-board
2pin_header__02 x 3
15pin_header__ x 2
atmega328
ftdi FT232rl
smt_resistor222 x 5
led x 4
16mhz crystal - measured
MINIUSBSHELL
MINIUSBCORE
MINI USB CONTACT x 5
cap106C x 2
reset core
reset shell
nano - reg
NANO DIODE
189 RESISTOR PACK
102 RESISTOR PACK

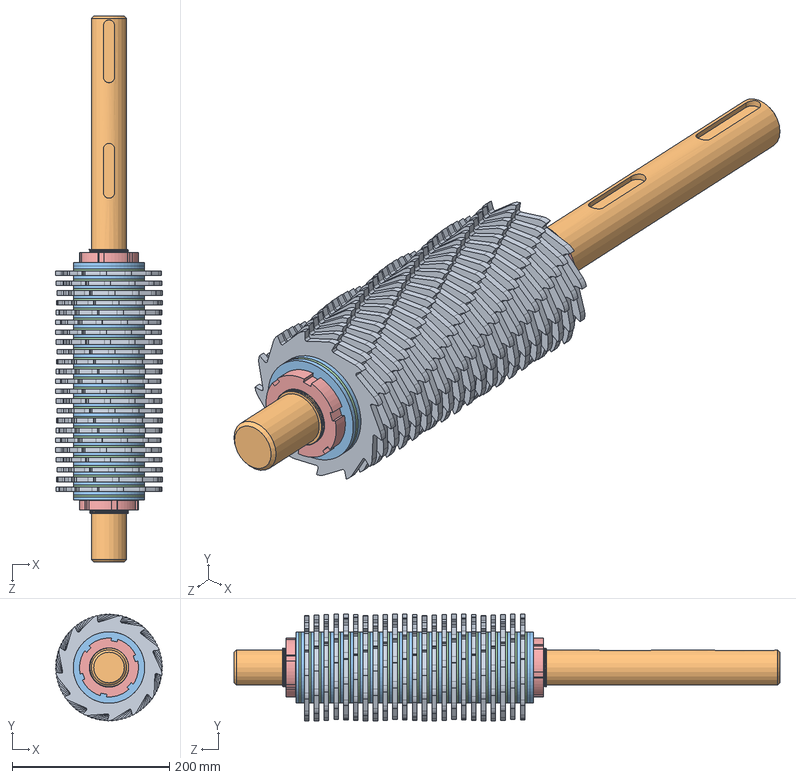
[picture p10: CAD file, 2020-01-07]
3. Build the machine/Shredder-Pro-Files/1 - 3D CAD/Shredder Solidworks CAD/SHRPRO-V1 1130.00-A Shaft 2 assembly.sldasm
136.0 x 135.9 x 695.0 mm
SHRPRO-V1 1130.01-A 13 Teeth blade x 23
SHRPRO-V1 1130.02-A Shaft 2
SHRPRO-V1 1120.14-A Spacer 4mm x 26
SHRPRO-V1 1120.15-A Spacer 2,5mm x 24
SHRPRO-V1 DIN 1804 M50x1,5 Slotted round nut x 2

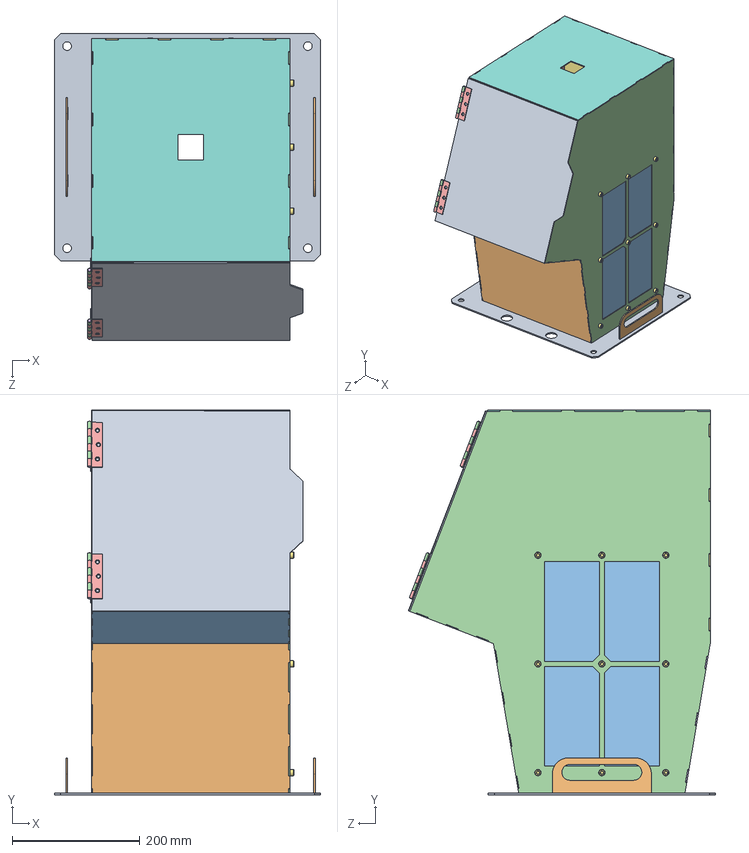
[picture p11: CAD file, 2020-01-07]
3. Build the machine/Upgrades/Safety Hopper/1 - 3D CAD/Solidworks CAD/SHRPRO-V1 1300.00-A Safety Hopper assembly.SLDASM
416.5 x 602.0 x 480.6 mm
SHRPRO-V1 1300.01-A Hopper botton plate
SHRPRO-V1 1300.02-A Hopper front plate 1
SHRPRO-V1 1300.03-A Hopper front plate 2
SHRPRO-V1 1300.04-A Hopper window side plate
SHRPRO-V1 1300.05-A Hopper side plate
SHRPRO-V1 1300.06-A Hopper back plate 1
SHRPRO-V1 1300.07-A Hopper back plate 2
SHRPRO-V1 1300.08-A Hopper top plate
SHRPRO-V1 1300.09-A Hopper door plate
SHRPRO-V1 1300.10-A Hopper handle x 2
SHRPRO-V1 1300.11-A Hopper window
52-1-3990_01 v2.2 x 2
52-1-3990_02 v2.2 x 2
52-1-3990_03 v2.2 x 2
socket head cap screw_din x 9
hex nut gradec_din x 9
plain washer normal grade c_iso x 9

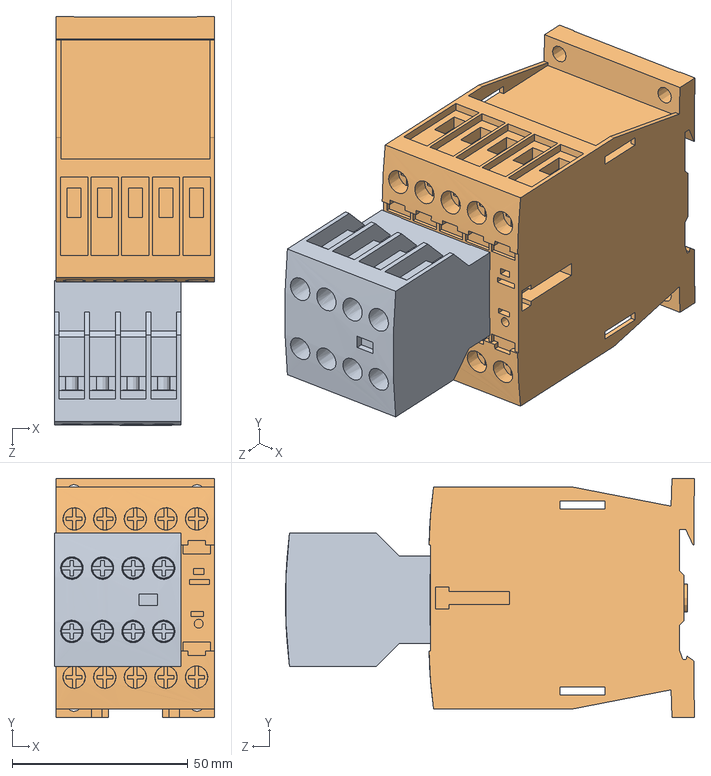
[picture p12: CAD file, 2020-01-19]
3. Build the machine/Shredder-Pro-Files/1 - 3D CAD/Shredder Solidworks CAD/00 - Commercial parts/Electronics/Contactor/SHRPRO-V1 18 EATON DILM contactor,4kW 230Vac 1break contact.SLDASM
45.5 x 68.0 x 116.3 mm
dilm32-xhi22
dilm9-01_230v50hz240v60hz_

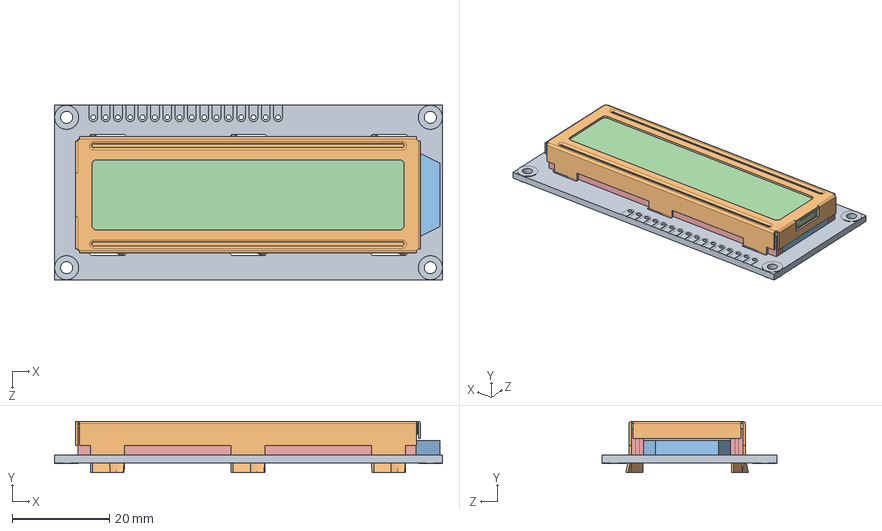
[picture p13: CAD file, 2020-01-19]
3. Build the machine/Shredder-Pro-Files/1 - 3D CAD/Shredder Solidworks CAD/00 - Commercial parts/Electronics/LCD Screen/16x2-character-lcd-display-1.snapshot.2/DFRobot_1602_LCD.SLDASM
80.0 x 10.6 x 36.0 mm
LCD_PCB
metal_casing
LCDbacklight
LCD
conductors x 2

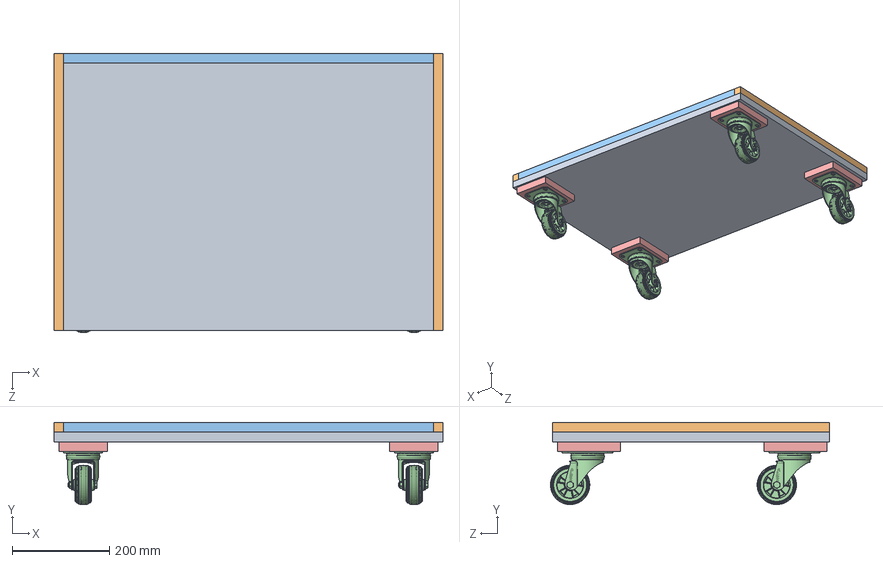
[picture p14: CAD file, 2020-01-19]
3. Build the machine/Shredder-Pro-Files/1 - 3D CAD/Shredder Solidworks CAD/00 - Commercial parts/Trolley/Trolley.SLDASM
800.0 x 168.9 x 574.0 mm
Trolley base
Trolley side x 2
Trolley side_2
CAD-2-0857.step x 4
Trolley spacer x 4

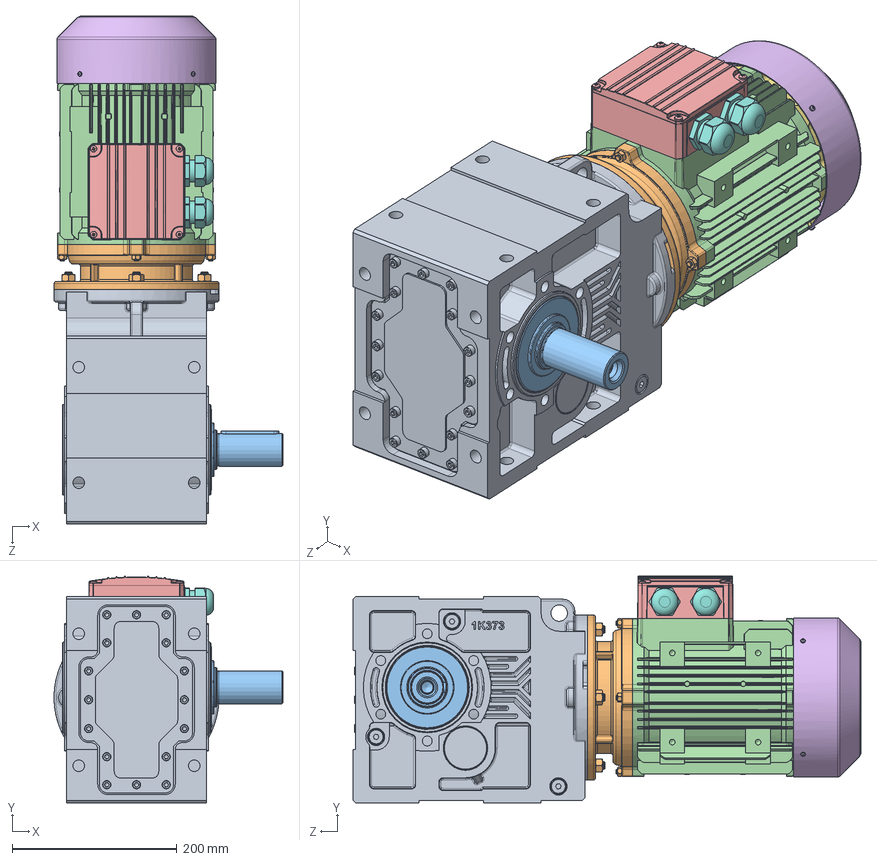
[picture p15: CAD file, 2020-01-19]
3. Build the machine/Shredder-Pro-Files/1 - 3D CAD/Shredder Solidworks CAD/00 - Commercial parts/Motor 2,2kW 373 Gearbox/SHRPRO-V1 04 2,2kW Motor KR 373 L3E100L.sldasm
277.4 x 274.9 x 615.8 mm
K373_Varsay_lan
333E100_Varsay_lan
ML15A_L_Varsay_lan
3E100L_DA_Varsay_lan
KL_3E100_Varsay_lan
T_3E100_1_Varsay_lan
EF2100A_Varsay_lan
RK_3E100_Varsay_lan

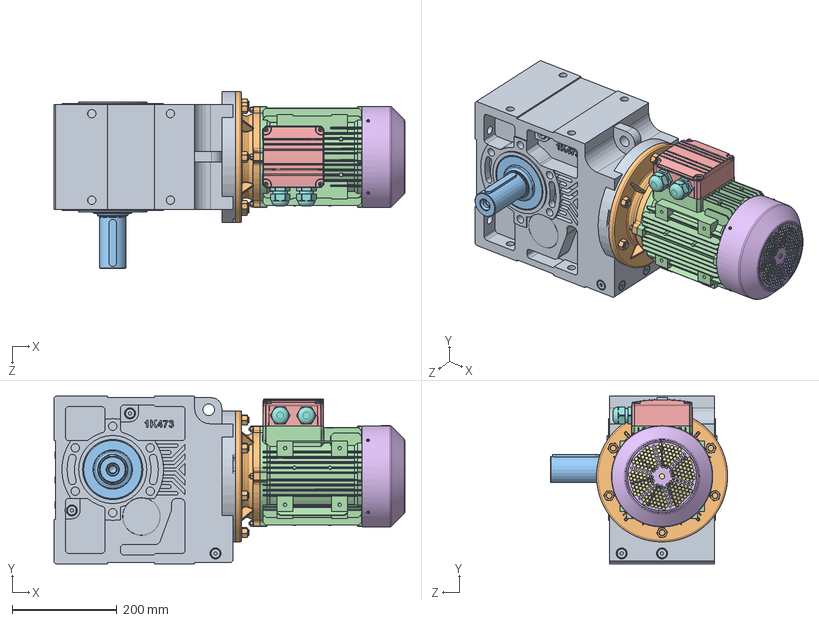
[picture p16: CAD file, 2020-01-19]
3. Build the machine/Shredder-Pro-Files/1 - 3D CAD/Shredder Solidworks CAD/00 - Commercial parts/Motor 3kW 473 Gearbox/SHRPRO-V1 3kW Motor KR 473 L3E100L.SLDASM
669.3 x 320.0 x 338.0 mm
K473_Varsay_lan
433E100_Varsay_lan
ML36A_L_Varsay_lan
3E100L_DA_Varsay_lan(2)
KL_3E100_Varsay_lan(2)
T_3E100_1_Varsay_lan(2)
EF2100A_Varsay_lan(2)
RK_3E100_Varsay_lan(2)

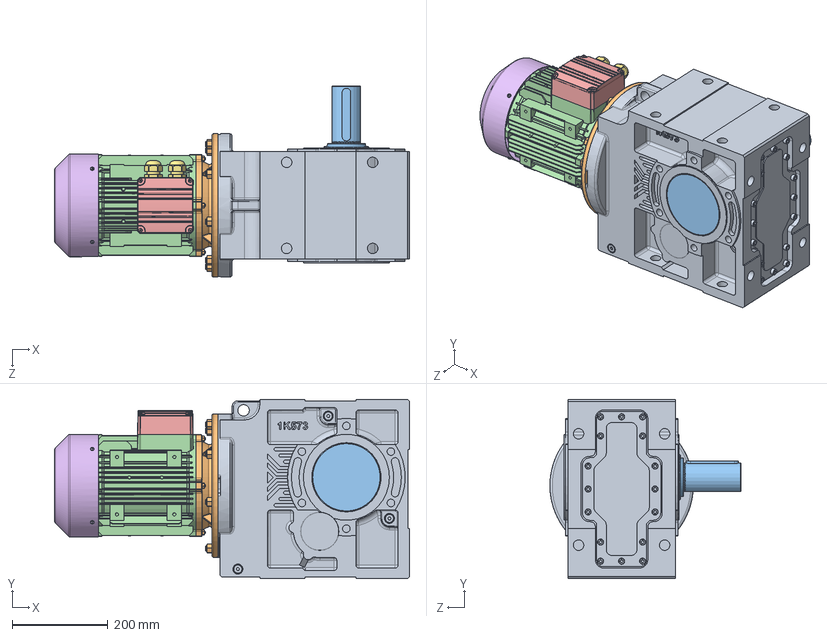
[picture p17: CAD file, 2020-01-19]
3. Build the machine/Shredder-Pro-Files/1 - 3D CAD/Shredder Solidworks CAD/00 - Commercial parts/Motor 4kW 573 Gearbox/SHRPRO-V1 4kW Motor KR573 L3E112M.SLDASM
742.6 x 375.0 x 400.0 mm
K573_Varsay_lan(2)
533E112_Varsay_lan
ML5A_L_Varsay_lan(2)
3E112M_DA_Varsay_lan
KL_3E112_Varsay_lan
T_3E112_1_Varsay_lan
RK_3E112_Varsay_lan

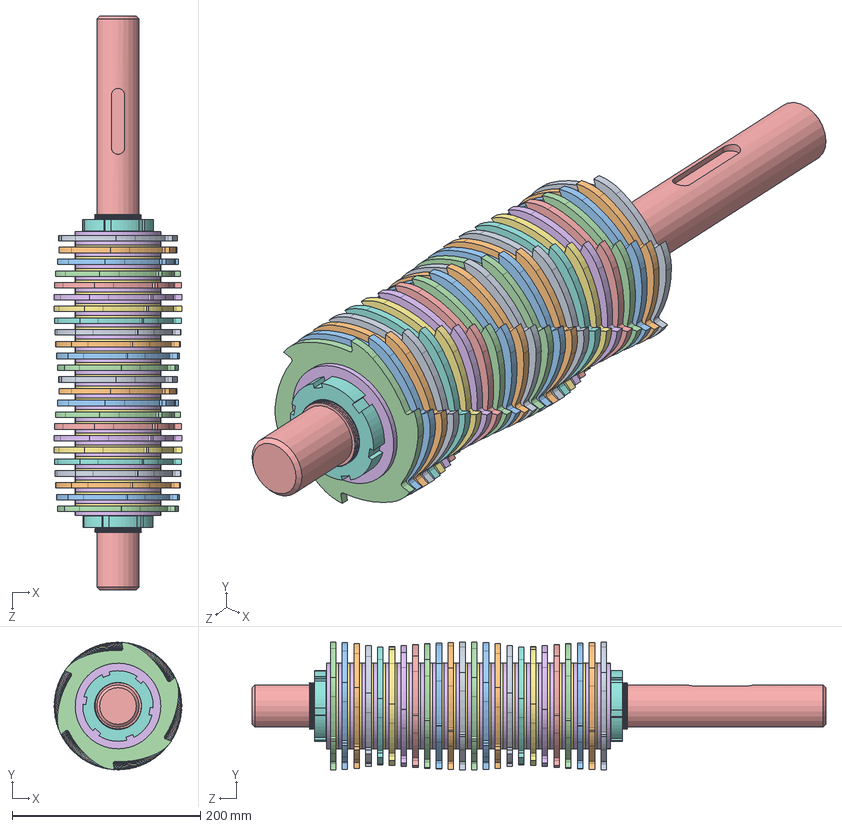
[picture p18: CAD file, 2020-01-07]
3. Build the machine/Shredder-Pro-Files/1 - 3D CAD/Shredder Solidworks CAD/SHRPRO-V1 1120.00-A Shaft 1 assembly.sldasm
135.9 x 135.9 x 610.0 mm
SHRPRO-V1 1120.01-A 6 Teeth blade 1 x 2
SHRPRO-V1 1120.02-A 6 Teeth blade 2 x 2
SHRPRO-V1 1120.03-A 6 Teeth blade 3 x 2
SHRPRO-V1 1120.04-A 6 Teeth blade 4 x 2
SHRPRO-V1 1120.05-A 6 Teeth blade 5 x 2
SHRPRO-V1 1120.06-A 6 Teeth blade 6 x 2
SHRPRO-V1 1120.07-A 6 Teeth blade 7 x 2
SHRPRO-V1 1120.08-A 6 Teeth blade 8 x 2
SHRPRO-V1 1120.09-A 6 Teeth blade 9 x 2
SHRPRO-V1 1120.10-A 6 Teeth blade 10 x 2
SHRPRO-V1 1120.11-A 6 Teeth blade 11 x 2
SHRPRO-V1 1120.12-A 6 Teeth blade 12 x 2
SHRPRO-V1 1120.13-A Shaft 1
SHRPRO-V1 1120.14-A Spacer 4mm x 25
SHRPRO-V1 1120.15-A Spacer 2,5mm x 23
SHRPRO-V1 DIN 1804 M50x1,5 Slotted round nut x 2

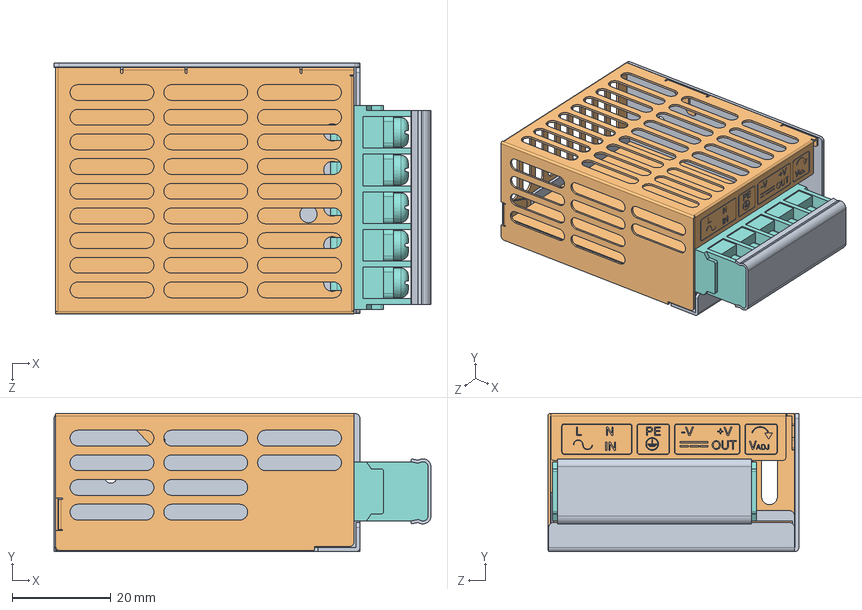
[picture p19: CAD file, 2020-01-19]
3. Build the machine/Shredder-Pro-Files/1 - 3D CAD/Shredder Solidworks CAD/00 - Commercial parts/Electronics/5V Power Supply 15W/txl_015-05s.SLDASM
76.4 x 28.0 x 50.9 mm
txl_015-05s_01
txl_015-05s_02
txl_015-05s_03
txl_015-05s_04
txl_015-05s_05
txl_015-05s_06
txl_015-05s_07
txl_015-05s_08
txl_015-05s_09
txl_015-05s_10
txl_015-05s_11
txl_015-05s_12
txl_015-05s_13
txl_015-05s_14
txl_015-05s_15
txl_015-05s_16
txl_015-05s_17
txl_015-05s_18

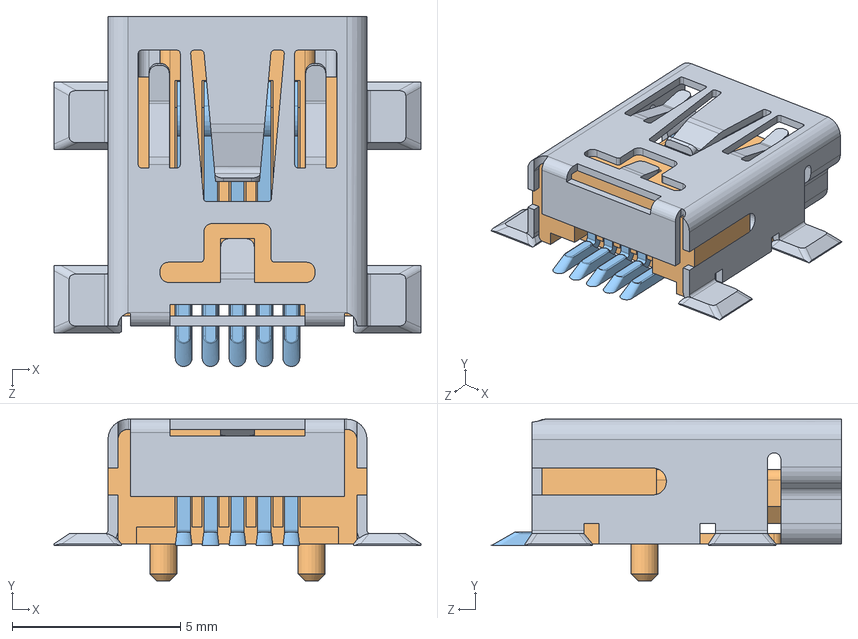
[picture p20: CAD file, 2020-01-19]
3. Build the machine/Shredder-Pro-Files/1 - 3D CAD/Shredder Solidworks CAD/00 - Commercial parts/Electronics/Arduino Nano/MINIUSB - MEASURED.SLDASM
10.9 x 4.80 x 10.4 mm
MINIUSBSHELL
MINIUSBCORE
MINI USB CONTACT x 5

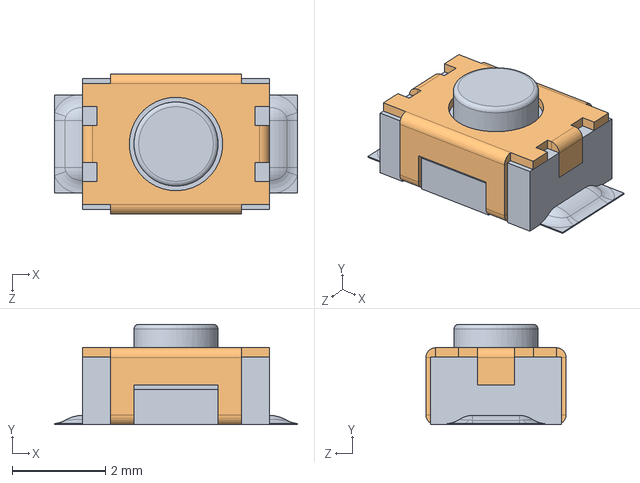
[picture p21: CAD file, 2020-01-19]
3. Build the machine/Shredder-Pro-Files/1 - 3D CAD/Shredder Solidworks CAD/00 - Commercial parts/Electronics/Arduino Nano/reset button.SLDASM
5.20 x 2.15 x 3.00 mm
reset core
reset shell

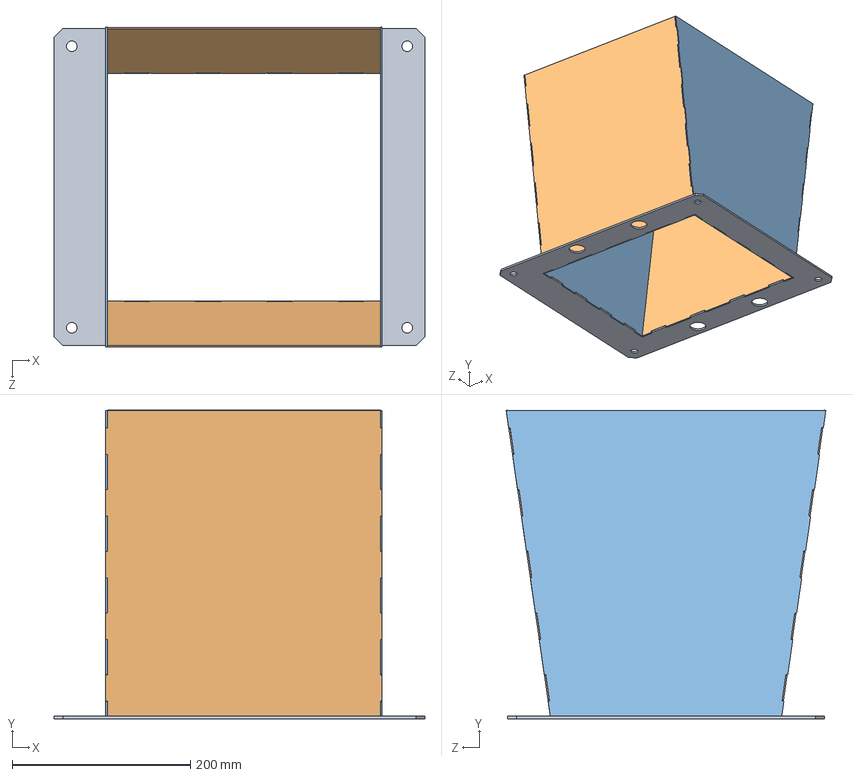
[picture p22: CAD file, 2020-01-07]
3. Build the machine/Shredder-Pro-Files/1 - 3D CAD/Shredder Solidworks CAD/SHRPRO-V1 1200.00-A Basic Hopper assembly.SLDASM
416.5 x 346.6 x 359.1 mm
SHRPRO-V1 1200.01-A Botton plate hopper
SHRPRO-V1 1200.02-A Front plate hopper x 2
SHRPRO-V1 1200.03-A Right plate hopper x 2

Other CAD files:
3. Build the machine/Shredder-Pro-Files/1 - 3D CAD/Shredder Solidworks CAD/SHRPRO-V1 1410.00-A Frame.sldasm
3. Build the machine/Shredder-Pro-Files/1 - 3D CAD/Shredder Solidworks CAD/SHRPRO-V1 1140.00-A Sieve.sldasm
3. Build the machine/Shredder-Pro-Files/1 - 3D CAD/Shredder Solidworks CAD/00 - Commercial parts/Bearing/SHRPRO-V1 UCFL 209 bearing.SLDPRT
3. Build the machine/Shredder-Pro-Files/1 - 3D CAD/Shredder Solidworks CAD/00 - Commercial parts/Coupling/SHRPRO-V1 03 Taper lock 3020-40.SLDPRT
3. Build the machine/Shredder-Pro-Files/1 - 3D CAD/STEP/SHRPRO-V1 1000.01-A Coupling cover.step
3. Build the machine/Shredder-Pro-Files/1 - 3D CAD/STEP/SHRPRO-V1 1000.02-A Bearing-coupling spacer 10mm.step
3. Build the machine/Shredder-Pro-Files/1 - 3D CAD/STEP/SHRPRO-V1 1000.03-A Bearing-coupling spacer 1mm.step
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

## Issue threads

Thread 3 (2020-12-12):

Quantity for Shredder pro file renaming

darigovresearch, 2020-12-12:
Having the Laser files have the quantities within the filename like in the non-pro versions or the main starter kit would be really helpful for users who download this kit. This would significantly improve the usability of this kit for the builders of the machines and potential local laser shops as they would not need to correlate the quantities with the PDFs.

Specifically having the files which are in [precious-plastic-starterkit-shredder/3. Build the machine/Shredder-Pro-Files/2 - Laser cut files/](https://github.com/ONEARMY/precious-plastic-starterkit-shredder/tree/master/3.%20Build%20the%20machine/Shredder-Pro-Files/2%20-%20Laser%20cut%20files) to be replaced/renamed by the ones in the main kit here - [precious-plastic-kit/3. Build/5. Shredder Pro/Shredder Pro Files/2. Laser cut files/](https://github.com/ONEARMY/precious-plastic-kit/tree/master/3.%20Build/5.%20Shredder%20Pro/Shredder%20Pro%20Files/2.%20Laser%20cut%20files)

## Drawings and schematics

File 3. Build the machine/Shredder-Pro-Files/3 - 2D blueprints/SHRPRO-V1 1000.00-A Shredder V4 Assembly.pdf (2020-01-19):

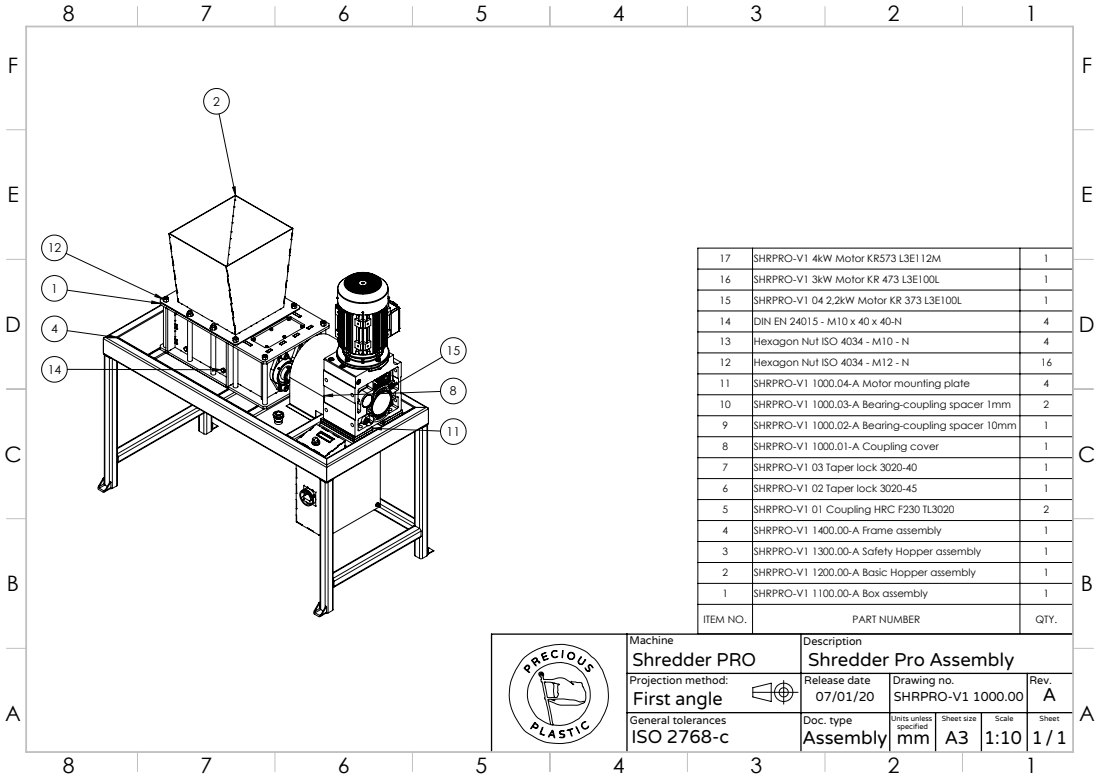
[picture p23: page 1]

17 | SHRPRO-V1 4kW Motor KR573 L3E112M | 1
16 | SHRPRO-V1 3kW Motor KR 473 L3E100L | 1
15 | SHRPRO-V1 04 2,2kW Motor KR 373 L3E100L | 1
14 | DIN EN 24015 - M10 x 40 x 40-N | 4
13 | Hexagon Nut ISO 4034 - M10 - N | 4
12 | Hexagon Nut ISO 4034 - M12 - N | 16
11 | SHRPRO-V1 1000.04-A Motor mounting plate | 4
10 | SHRPRO-V1 1000.03-A Bearing-coupling spacer 1mm | 2
9 | SHRPRO-V1 1000.02-A Bearing-coupling spacer 10mm | 1
8 | SHRPRO-V1 1000.01-A Coupling cover | 1
7 | SHRPRO-V1 03 Taper lock 3020-40 | 1
6 | SHRPRO-V1 02 Taper lock 3020-45 | 1
5 | SHRPRO-V1 01 Coupling HRC F230 TL3020 | 2
4 | SHRPRO-V1 1400.00-A Frame assembly | 1
3 | SHRPRO-V1 1300.00-A Safety Hopper assembly | 1
2 | SHRPRO-V1 1200.00-A Basic Hopper assembly | 1
1 | SHRPRO-V1 1100.00-A Box assembly | 1
ITEM NO. | PART NUMBER | QTY.

Machine Shredder PRO | Description Shredder Pro Assembly
Projection method: First angle | Release date 07/01/20 | Drawing no. SHRPRO-V1 1000.00 | Rev. A
General tolerances ISO 2768-c | Doc. type Assembly | Units unless specified mm | Sheet size A3 | Scale 1:10 | Sheet 1 / 1

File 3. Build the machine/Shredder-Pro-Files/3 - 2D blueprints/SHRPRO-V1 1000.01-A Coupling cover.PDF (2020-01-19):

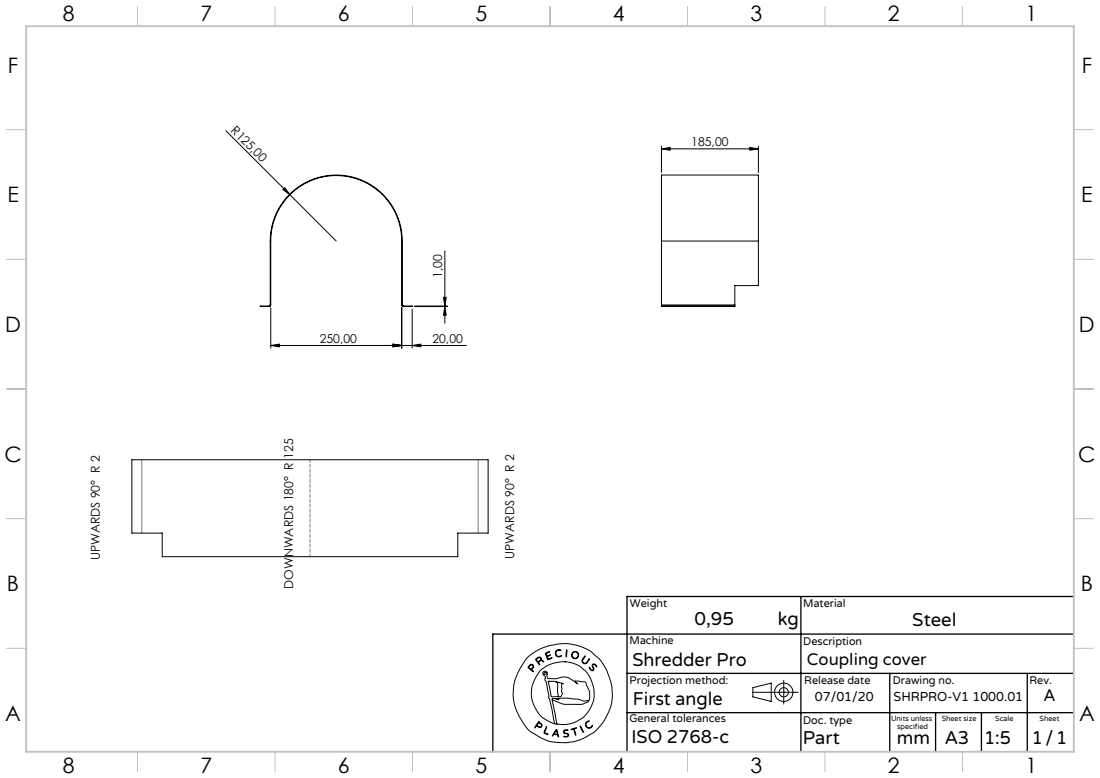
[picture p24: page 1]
DOWNWARDS 180° R 125; UPWARDS 90° R 2

Weight 0,95 kg | Material Steel

Machine Shredder Pro | Description Coupling cover
Projection method: First angle | Release date 07/01/20 | Drawing no. SHRPRO-V1 1000.01 | Rev. A
General tolerances ISO 2768-c | Doc. type Part | Units unless specified mm | Sheet size A3 | Scale 1:5 | Sheet 1 1 /

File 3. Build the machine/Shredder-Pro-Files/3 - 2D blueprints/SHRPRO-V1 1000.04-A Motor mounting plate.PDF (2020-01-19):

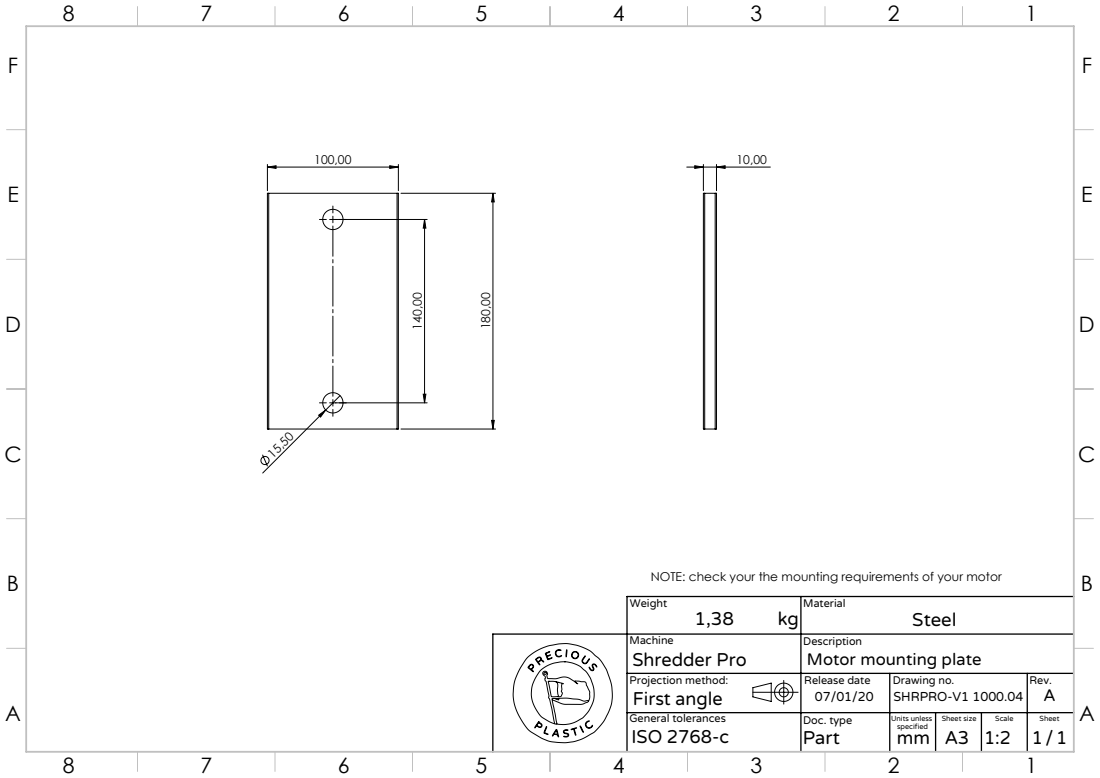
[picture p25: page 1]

NOTE: check your the mounting requirements of your motor

Weight 1,38 kg | Material Steel

Machine Shredder Pro | Description Motor mounting plate
Projection method: First angle | Release date 07/01/20 | Drawing no. SHRPRO-V1 1000.04 | Rev. A
General tolerances ISO 2768-c | Doc. type Part | Units unless specified mm | Sheet size A3 | Scale 1:2 | Sheet 1 1 /

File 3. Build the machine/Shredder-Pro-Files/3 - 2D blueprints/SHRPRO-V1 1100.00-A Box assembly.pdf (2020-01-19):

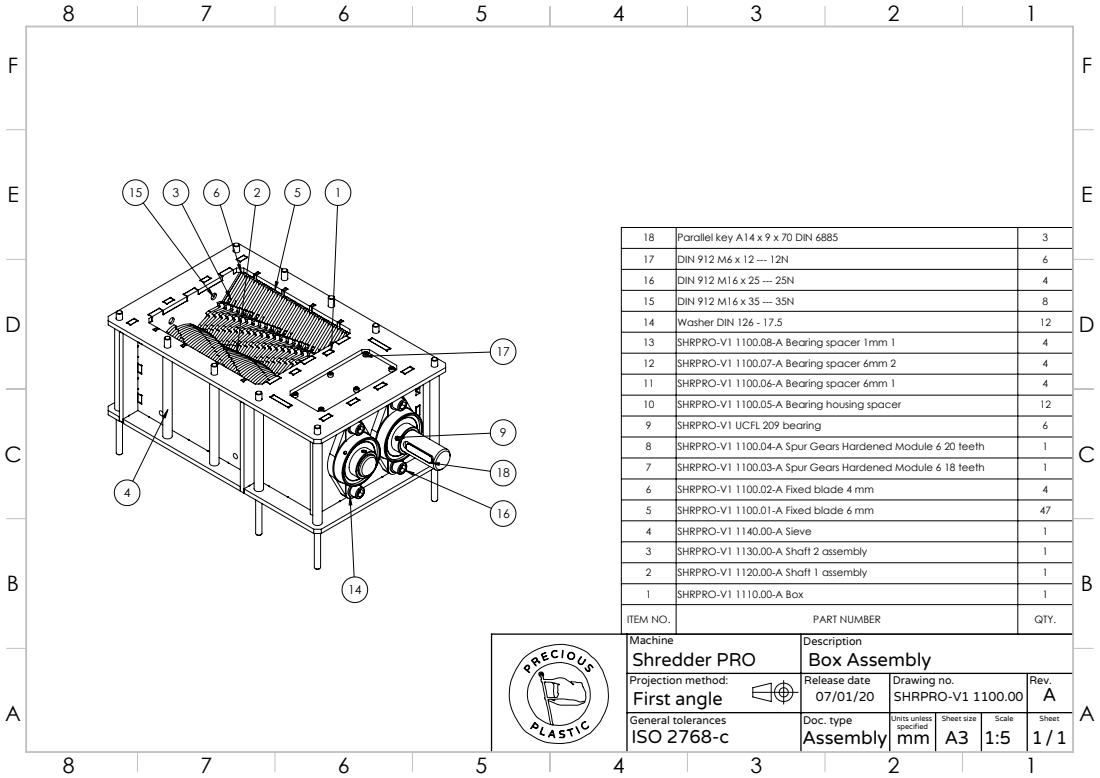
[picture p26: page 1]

18 | Parallel key A14 x 9 x 70 DIN 6885 | 3
17 | DIN 912 M6 x 12 --- 12N | 6
16 | DIN 912 M16 x 25 --- 25N | 4
15 | DIN 912 M16 x 35 --- 35N | 8
14 | Washer DIN 126 - 17.5 | 12
13 | SHRPRO-V1 1100.08-A Bearing spacer 1mm 1 | 4
12 | SHRPRO-V1 1100.07-A Bearing spacer 6mm 2 | 4
11 | SHRPRO-V1 1100.06-A Bearing spacer 6mm 1 | 4
10 | SHRPRO-V1 1100.05-A Bearing housing spacer | 12
9 | SHRPRO-V1 UCFL 209 bearing | 6
8 | SHRPRO-V1 1100.04-A Spur Gears Hardened Module 6 20 teeth | 1
7 | SHRPRO-V1 1100.03-A Spur Gears Hardened Module 6 18 teeth | 1
6 | SHRPRO-V1 1100.02-A Fixed blade 4 mm | 4
5 | SHRPRO-V1 1100.01-A Fixed blade 6 mm | 47
4 | SHRPRO-V1 1140.00-A Sieve | 1
3 | SHRPRO-V1 1130.00-A Shaft 2 assembly | 1
2 | SHRPRO-V1 1120.00-A Shaft 1 assembly | 1
1 | SHRPRO-V1 1110.00-A Box | 1
ITEM NO. | PART NUMBER | QTY.
Machine Shredder PRO | Description Box Assembly
Projection method: First angle | Release date 07/01/20 | Drawing no. SHRPRO-V1 1100.00 | Rev. A
General tolerances ISO 2768-c | Doc. type Assembly | Units unless specified mm | Sheet size A3 | Scale 1:5 | Sheet 1 1 /

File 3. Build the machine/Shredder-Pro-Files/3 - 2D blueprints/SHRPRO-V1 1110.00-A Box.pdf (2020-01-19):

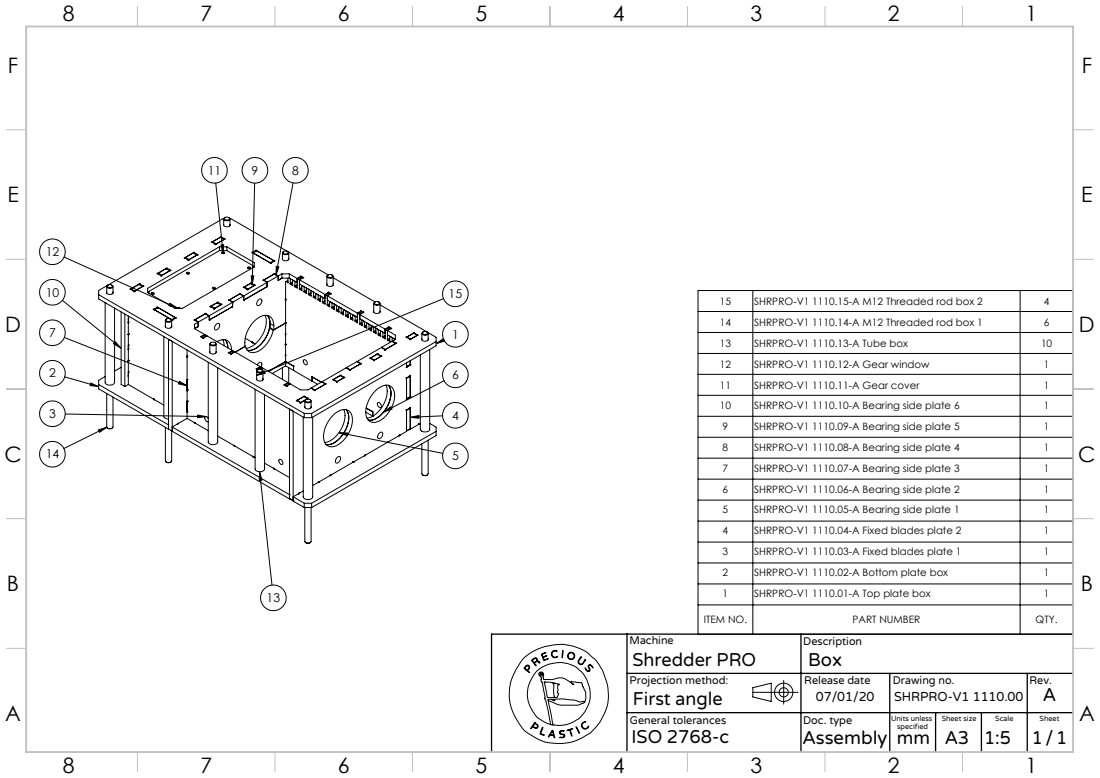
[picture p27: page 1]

15 | SHRPRO-V1 1110.15-A M12 Threaded rod box 2 | 4
14 | SHRPRO-V1 1110.14-A M12 Threaded rod box 1 | 6
13 | SHRPRO-V1 1110.13-A Tube box | 10
12 | SHRPRO-V1 1110.12-A Gear window | 1
11 | SHRPRO-V1 1110.11-A Gear cover | 1
10 | SHRPRO-V1 1110.10-A Bearing side plate 6 | 1
9 | SHRPRO-V1 1110.09-A Bearing side plate 5 | 1
8 | SHRPRO-V1 1110.08-A Bearing side plate 4 | 1
7 | SHRPRO-V1 1110.07-A Bearing side plate 3 | 1
6 | SHRPRO-V1 1110.06-A Bearing side plate 2 | 1
5 | SHRPRO-V1 1110.05-A Bearing side plate 1 | 1
4 | SHRPRO-V1 1110.04-A Fixed blades plate 2 | 1
3 | SHRPRO-V1 1110.03-A Fixed blades plate 1 | 1
2 | SHRPRO-V1 1110.02-A Bottom plate box | 1
1 | SHRPRO-V1 1110.01-A Top plate box | 1
ITEM NO. | PART NUMBER | QTY.

Machine Shredder PRO | Description Box
Projection method: First angle | Release date 07/01/20 | Drawing no. SHRPRO-V1 1110.00 | Rev. A
General tolerances ISO 2768-c | Doc. type Assembly | Units unless specified mm | Sheet size A3 | Scale 1:5 | Sheet 1 1 /

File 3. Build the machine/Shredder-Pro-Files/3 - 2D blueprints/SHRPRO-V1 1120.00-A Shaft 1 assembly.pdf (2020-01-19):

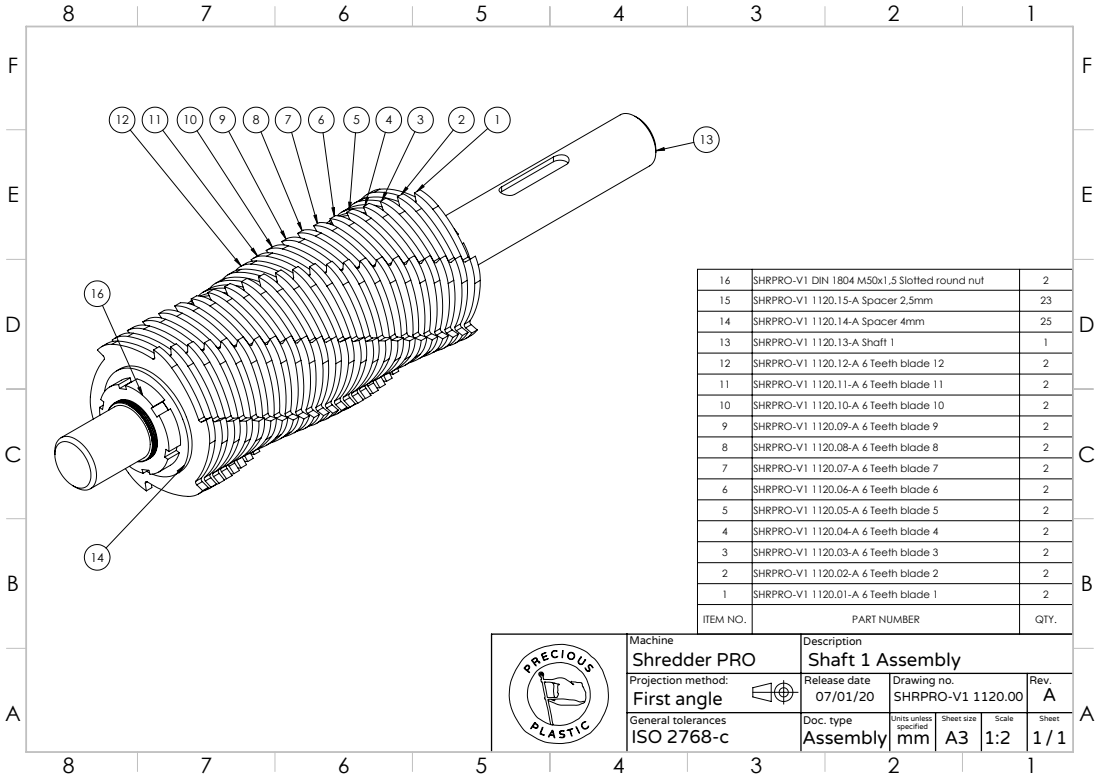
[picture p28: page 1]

16 | SHRPRO-V1 DIN 1804 M50x1,5 Slotted round nut | 2
15 | SHRPRO-V1 1120.15-A Spacer 2,5mm | 23
14 | SHRPRO-V1 1120.14-A Spacer 4mm | 25
13 | SHRPRO-V1 1120.13-A Shaft 1 | 1
12 | SHRPRO-V1 1120.12-A 6 Teeth blade 12 | 2
11 | SHRPRO-V1 1120.11-A 6 Teeth blade 11 | 2
10 | SHRPRO-V1 1120.10-A 6 Teeth blade 10 | 2
9 | SHRPRO-V1 1120.09-A 6 Teeth blade 9 | 2
8 | SHRPRO-V1 1120.08-A 6 Teeth blade 8 | 2
7 | SHRPRO-V1 1120.07-A 6 Teeth blade 7 | 2
6 | SHRPRO-V1 1120.06-A 6 Teeth blade 6 | 2
5 | SHRPRO-V1 1120.05-A 6 Teeth blade 5 | 2
4 | SHRPRO-V1 1120.04-A 6 Teeth blade 4 | 2
3 | SHRPRO-V1 1120.03-A 6 Teeth blade 3 | 2
2 | SHRPRO-V1 1120.02-A 6 Teeth blade 2 | 2
1 | SHRPRO-V1 1120.01-A 6 Teeth blade 1 | 2
ITEM NO. | PART NUMBER | QTY.

Machine Shredder PRO | Description Shaft 1 Assembly
Projection method: First angle | Release date 07/01/20 | Drawing no. SHRPRO-V1 1120.00 | Rev. A
General tolerances ISO 2768-c | Doc. type Assembly | Units unless specified mm | Sheet size A3 | Scale 1:2 | Sheet 1 1 /

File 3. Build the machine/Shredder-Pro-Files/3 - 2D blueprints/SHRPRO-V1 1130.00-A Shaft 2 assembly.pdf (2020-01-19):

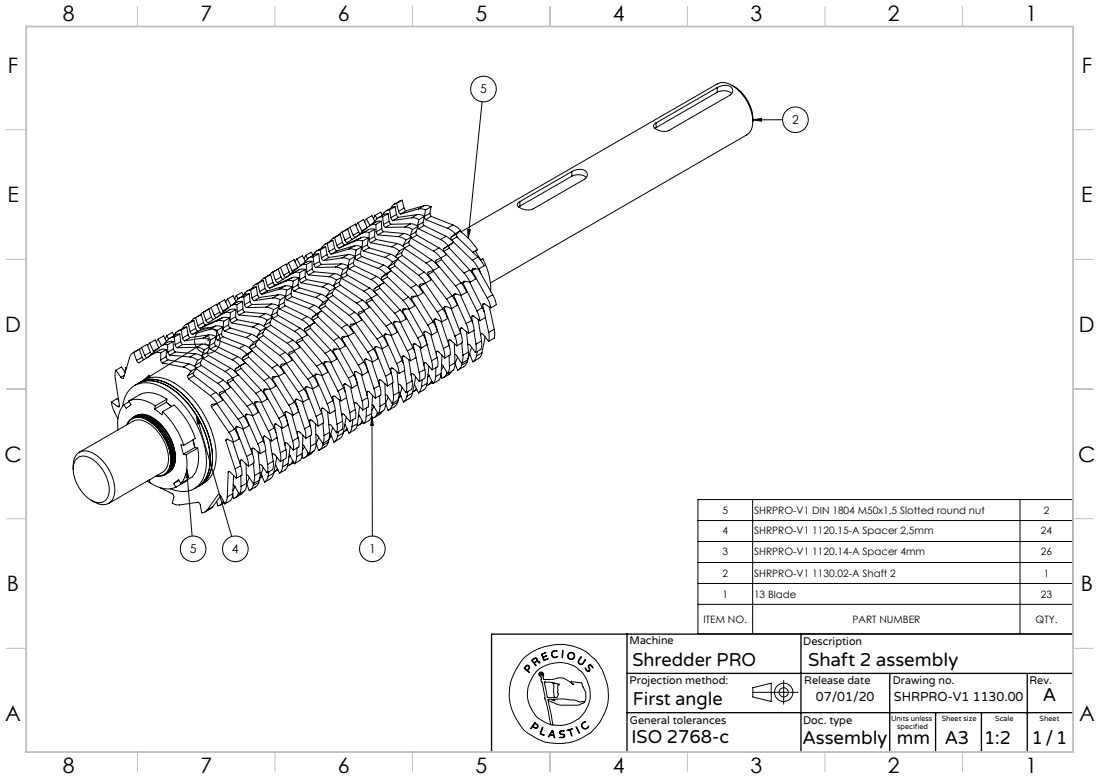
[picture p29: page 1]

5 | SHRPRO-V1 DIN 1804 M50x1,5 Slotted round nut | 2
4 | SHRPRO-V1 1120.15-A Spacer 2,5mm | 24
3 | SHRPRO-V1 1120.14-A Spacer 4mm | 26
2 | SHRPRO-V1 1130.02-A Shaft 2 | 1
1 | 13 Blade | 23
ITEM NO. | PART NUMBER | QTY.

Machine Shredder PRO | Description Shaft 2 assembly
Projection method: First angle | Release date 07/01/20 | Drawing no. SHRPRO-V1 1130.00 | Rev. A
General tolerances ISO 2768-c | Doc. type Assembly | Units unless specified mm | Sheet size A3 | Scale 1:2 | Sheet 1 1 /

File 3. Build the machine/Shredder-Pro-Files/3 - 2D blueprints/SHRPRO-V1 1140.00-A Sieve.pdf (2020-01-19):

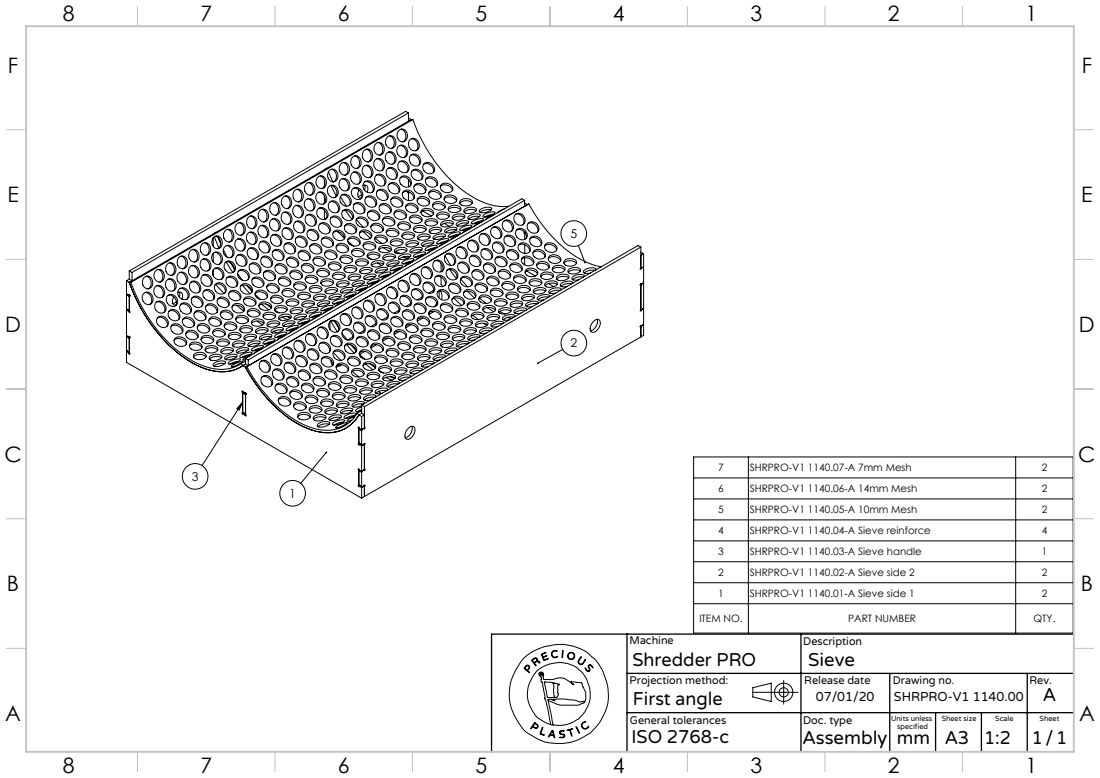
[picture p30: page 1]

7 | SHRPRO-V1 1140.07-A 7mm Mesh | 2
6 | SHRPRO-V1 1140.06-A 14mm Mesh | 2
5 | SHRPRO-V1 1140.05-A 10mm Mesh | 2
4 | SHRPRO-V1 1140.04-A Sieve reinforce | 4
3 | SHRPRO-V1 1140.03-A Sieve handle | 1
2 | SHRPRO-V1 1140.02-A Sieve side 2 | 2
1 | SHRPRO-V1 1140.01-A Sieve side 1 | 2
ITEM NO. | PART NUMBER | QTY.

Machine Shredder PRO | Description Sieve
Projection method: First angle | Release date 07/01/20 | Drawing no. SHRPRO-V1 1140.00 | Rev. A
General tolerances ISO 2768-c | Doc. type Assembly | Units unless specified mm | Sheet size A3 | Scale 1:2 | Sheet 1 1 /

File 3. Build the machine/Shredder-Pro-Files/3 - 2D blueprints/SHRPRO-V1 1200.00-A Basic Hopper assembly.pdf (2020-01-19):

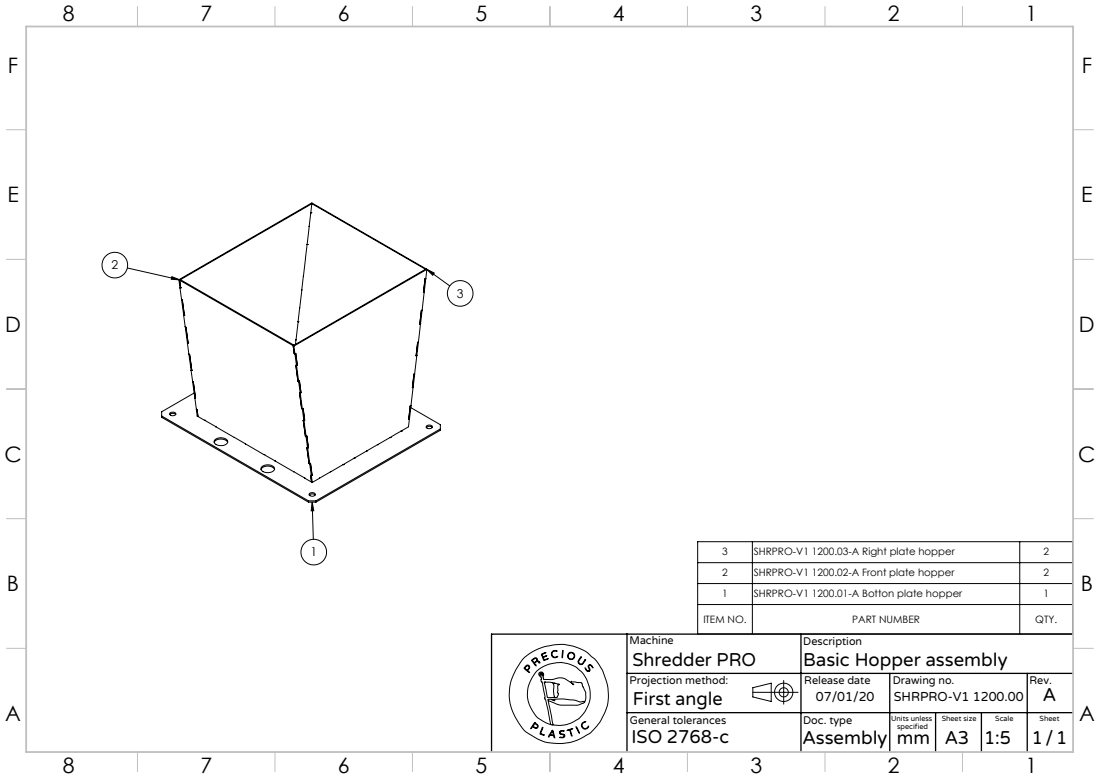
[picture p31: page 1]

3 | SHRPRO-V1 1200.03-A Right plate hopper | 2
2 | SHRPRO-V1 1200.02-A Front plate hopper | 2
1 | SHRPRO-V1 1200.01-A Botton plate hopper | 1
ITEM NO. | PART NUMBER | QTY.

Machine Shredder PRO | Description Basic Hopper assembly
Projection method: First angle | Release date 07/01/20 | Drawing no. SHRPRO-V1 1200.00 | Rev. A
General tolerances ISO 2768-c | Doc. type Assembly | Units unless specified mm | Sheet size A3 | Scale 1:5 | Sheet 1 1 /

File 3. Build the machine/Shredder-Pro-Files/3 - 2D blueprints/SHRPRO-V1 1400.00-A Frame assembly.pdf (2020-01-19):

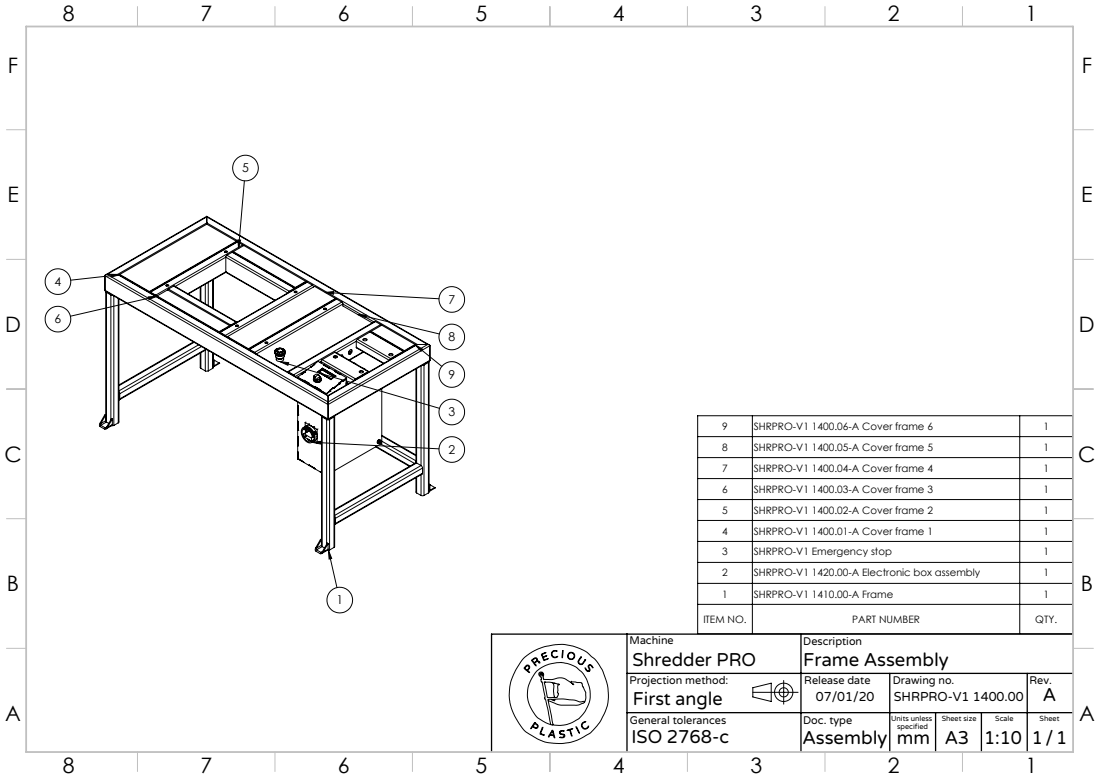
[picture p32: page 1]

9 | SHRPRO-V1 1400.06-A Cover frame 6 | 1
8 | SHRPRO-V1 1400.05-A Cover frame 5 | 1
7 | SHRPRO-V1 1400.04-A Cover frame 4 | 1
6 | SHRPRO-V1 1400.03-A Cover frame 3 | 1
5 | SHRPRO-V1 1400.02-A Cover frame 2 | 1
4 | SHRPRO-V1 1400.01-A Cover frame 1 | 1
3 | SHRPRO-V1 Emergency stop | 1
2 | SHRPRO-V1 1420.00-A Electronic box assembly | 1
1 | SHRPRO-V1 1410.00-A Frame | 1
ITEM NO. | PART NUMBER | QTY.

Machine Shredder PRO | Description Frame Assembly
Projection method: First angle | Release date 07/01/20 | Drawing no. SHRPRO-V1 1400.00 | Rev. A
General tolerances ISO 2768-c | Doc. type Assembly | Units unless specified mm | Sheet size A3 | Scale 1:10 | Sheet 1 1 /

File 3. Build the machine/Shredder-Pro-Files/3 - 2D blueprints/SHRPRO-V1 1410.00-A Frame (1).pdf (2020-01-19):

E | E
F | F

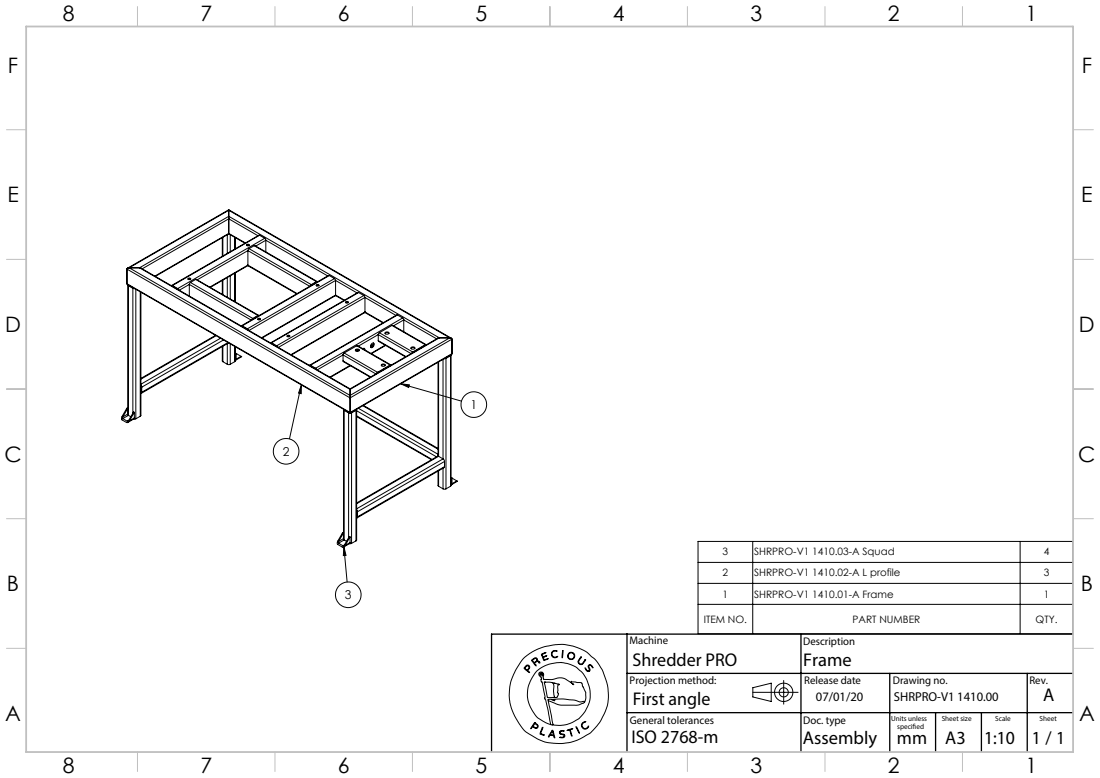
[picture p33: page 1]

3 | SHRPRO-V1 1410.03-A Squad | 4
2 | SHRPRO-V1 1410.02-A L profile | 3
1 | SHRPRO-V1 1410.01-A Frame | 1
ITEM NO. | PART NUMBER | QTY.

Machine Shredder PRO | Description Frame
Projection method: First angle | Release date 07/01/20 | Drawing no. SHRPRO-V1 1410.00 | Rev. A
General tolerances ISO 2768-m | Doc. type Assembly | Units unless specied mm | Sheet size A3 | Scale 1:10 | Sheet 1 1 /

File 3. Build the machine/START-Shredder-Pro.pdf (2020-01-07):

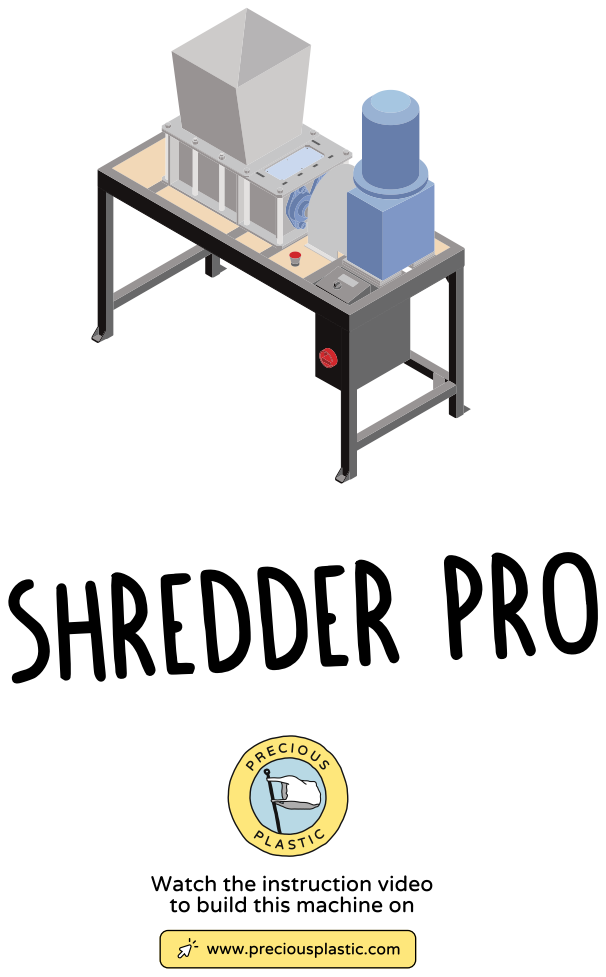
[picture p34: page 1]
shredder Pro

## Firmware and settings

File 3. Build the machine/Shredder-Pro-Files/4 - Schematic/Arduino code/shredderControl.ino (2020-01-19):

/*
  this sketch lets an ac induction motor switch direction
  at the push of a three-state button: forward, reverse and stop. And there's a big switch that switches off everything.
  There's a safety in the wiring that makes sure both directions cannot switch on both at once,
  but the arduino wouldn't do that either.
  This sketch also monitors the current through the motor with a Hall sensor. If the current rises above a set limit,
  the machine will register a jam. It will turn back for a second and try again for a set amount of times. If it continues
  to be jammed it switches off.
  Oh and it also makes use of a display to tell the world how it is doing.
  It is possible to use the serial plotter to monitor current, since that is the only number that is dumped on serial.
*/

#include <EEPROM.h>
#include <LiquidCrystal_I2C.h>            //use the LCD Display (yes it is one of those i2c things)
#include <Wire.h>

//#define DEBUG 1

#define SHRED_ST  0             // Shredding state Stopped
#define SHRED_FW  1             // Shredding state Forward
#define SHRED_REV 2             // Shredding state Reversing

#define JAMMED_NO 0             // Not jammed state
#define JAMMED_YE 1             // Jammed detected state: waiting for motor to loose inertia
#define JAMMED_RV 2             // Reversing after jammed state
#define JAMMED_RE 3             // Jamming reverse done state: waiting for motor to loose inertia

#define A_2_AREAD(c) (runConf.v0A + (c/AnalogR2A))
#define AREAD_2_A(c) ((c - runConf.v0A)*AnalogR2A)
const float AnalogR2A = 5.0 / (1024 * 0.066);

/* Configuration, you can adjust this via serial */
#define EEPROM_ID "PPS"
#define EEPROM_V 0

#define D_V0A 538                   // Tune this value to Analog read when no current flowing
#define D_START_SPAN 500            // Time to ignore current spikes due to motor start
#define D_MAX_JAMS 3                // Max amount of jams in a set time
#define D_MIN_JAM_TIME 15000        // That time in milliseconds
#define E_UNJAM_REVERSE_T 3000      // Retraction time to unjam
#define MAX_CURRENT 12              // Max current in Amps, to detect jams

struct ShredderConf {
  int v0A;
  int startSpan;
  int maxJams;
  int minJamTime;
  int unjamReverseT;
  int maxCurrent;   // this is the value over which the hall sensor signal will register as a jam.
};
ShredderConf runConf;
/* Config end */

// constants won't change. They're used here to set pin numbers:
const int shredButton = 7;     // the number of the pin that registers if you want the machine to shred
const int reverseButton = 6;   // the number of the pin that registers if you want the machine to reverse
const int motionPin = 4;       // the number of the pin that decides if the motor turns
const int directionPin = 3;    // the number of the pin that decides the driection of the motor
const int measurePin = A0;     // this pin has a hall sensor connected to it that measures the output current to the motor

int jamState = JAMMED_NO;
unsigned long jamTick;

unsigned long jamTime = 0;     // this int will store time between problematic jams
int current;                   // this int will store the measured current
int jammedCounter = 0;         // this int will store the amount of Jams within the minJamTime
unsigned long startTime = 0;   // this int is needed to count the interval between jams.
int i;

boolean working = true;
boolean configMode = false;
boolean alarmed = false;
unsigned long lastStart = 0;
unsigned long lastCurrentPrint = 0;
float currentAvg = 0;
int currentCount = 0;
int shredDir = SHRED_ST;

LiquidCrystal_I2C lcd(0x3F, 16, 2);           //set the address and dimensions of the LCD. Here the address is 0x3F, but it depends on the chip. You can use and i2c-scanner to determine the address of your chip.

byte pBar[8] = {0x1f, 0x1f, 0x1f, 0x1f, 0x1f, 0x1f, 0x1f, 0x1f};

String inputString = "";         // a String to hold incoming data
char * banner = "Precious Plastic v4";
char lcdBuffer[16];
///So here comes what the machine will do on startup
void setup() {
  analogReference(EXTERNAL);      //Use external reference for ADC
  // initialize the output pins:
  pinMode(motionPin, OUTPUT);
  digitalWrite(motionPin, HIGH);  //STOP shredder at boot //TODO: change from inverted to normal logic: HIGH -> ON
  pinMode(directionPin, OUTPUT);
  // initialize input pins:
  pinMode(shredButton, INPUT);
  pinMode(reverseButton, INPUT);
  pinMode(measurePin, INPUT);

  Serial.begin(115200);
  //initialise the lcd
  lcd.init();
  lcd.createChar(0, pBar);
  lcd.setBacklight(HIGH);
  lcd.setCursor(0, 1);
  lcd.print("Shredder Pro  ");
  for (int i = 0; i < 4; i++) {
    lcd.setCursor(0, 0);
    sprintf(lcdBuffer, "%.16s", &(banner[i]));
    //lcd.print(&(banner[i]);
    lcd.print(lcdBuffer);
    delay(350);
  }
  readConfig();
  delay(1000);
  lcd.setCursor(0, 1);
  lcd.print("             ");
  inputString.reserve(50);
}

// here comes what the machine will do while running, which is basically shred, reverse or do nothing
void loop() {
  if(configMode)return; //Do noting while in config mode
  current = analogRead(measurePin);
  checkDirection();
  if (!alarmed) {
    if (jamState == JAMMED_NO) {
      if (working && millis() >= lastStart + runConf.startSpan && current > runConf.maxCurrent) {
        halt();                                    // the machine stops
        countJams();                               // count how often this happens within an unacceaptable timeframe
        if (jammedCounter >= runConf.maxJams) {
          alarm();                                 // If it has jammed too much in timeframe stop everything
        } else {
          jamTick  = millis();
          jamState = JAMMED_YE;
        }
      }
    }
    switch (jamState) {
      case JAMMED_YE:
        if ((current <= runConf.v0A + 2) || (millis() > jamTick + 2000)) {      // wait a bit to make the shredder halt
          reverse();                               // then it reverses
          jamTick  = millis();
          jamState = JAMMED_RV;
        }
        break;
      case JAMMED_RV:
        if (millis() > jamTick + runConf.unjamReverseT) {          // Reverse for set amount and stop
          halt();
          jamTick  = millis();
          jamState = JAMMED_RE;
        }
        break;
      case JAMMED_RE:
        if ((current <= runConf.v0A + 2) || (millis() > jamTick + 3000)) {      // Let the motor come to a halt
          jamState = JAMMED_NO;
          if (shredDir == SHRED_FW)
            shred();
          else
            reverse();      //On reversed jam stop and try again
        }
        break;
      default:
        break;
    }
    printCurrent();      // display this as value in amps.
    printBar();          //displays current as a progress bar.
    //printValue();      //you can also display the measured value.
  }
#ifndef DEBUG
  Serial.println(AREAD_2_A(current));             // You can read the current over serial
#endif
}

void serialEvent() {
  while (Serial.available()) {
    char inChar = (char)Serial.read();
    inputString += inChar;
    if (inChar == '\n') {
      if(configMode){
        //TODO: receive config vars and store to EEPROM
        int v,r_v0A, r_startSpan, r_maxJams, r_minJamTime, r_unjamReverseT, r_maxCurrent;
        int decoded = sscanf(const_cast<char*>(inputString.c_str()), "%d,%d,%d,%d,%d,%d,%d", &v, &r_v0A, &r_startSpan, &r_maxJams, &r_minJamTime, &r_unjamReverseT, &r_maxCurrent);
        if(decoded != 7){
          Serial.print("Invalid config received: ");
          Serial.println(inputString);
        }else{
          if(v!=EEPROM_V){
            Serial.println("Config version received doesn't match firmware");
          }else{
            runConf = {
              r_v0A,
              r_startSpan,
              r_maxJams,
              r_minJamTime,
              r_unjamReverseT,
              0
            };
            runConf.maxCurrent = A_2_AREAD(r_maxCurrent); //Max current should be calculated after we have loaded config voltage offset for 0A(v0A)
            saveConfig();
            configMode = false;
            Serial.println("config ok");
          }
        }
      }
      if(inputString.equals("config\n")){
        digitalWrite(motionPin, HIGH);                        // Switch it all off
        Serial.println("Entering config mode");
        configMode = true;
        working = false;
        lcd.setCursor(0, 0);
        lcd.print("PP Shredder     ");
        lcd.setCursor(0, 1);
        lcd.print("     config mode");
      }
      if(inputString.equals("reset\n")){
        Serial.println("Restoring default config");
        restoreConfig();
      }
#ifdef DEBUG
      Serial.print("Received: ");Serial.println(inputString);
#endif
      inputString = "";
    }
  }
}

void shred() {
  lcd.setCursor(0, 0);
  lcd.print("Shredding  ");
#ifdef DEBUG
  Serial.println("Shredding");
#endif
  digitalWrite(motionPin, LOW);                          // set stuff in motion
  digitalWrite(directionPin, LOW);                        // in the forward direction
}

void reverse() {
  lcd.setCursor(0, 0);
  lcd.print("Reversing  ");
#ifdef DEBUG
  Serial.println("I am going back");
#endif
  digitalWrite(motionPin, LOW);                        // Set stuff in motion
  digitalWrite(directionPin, HIGH);                          // in the reverse direction
}

void halt() {
  lcd.setCursor(0, 0);
  lcd.print("Shredder   ");
#ifdef DEBUG
  Serial.println("STOP");   //tell the world you are coming to a halt
#endif
  digitalWrite(motionPin, HIGH);                        // Switch it all off
}

void countJams() {
#ifdef DEBUG
  Serial.print(startTime);
  Serial.print(" vs ");
  Serial.println(millis());
#endif
  if (startTime == 0) {
    jamTime = runConf.minJamTime;                 //If it is the first time, don't mind elapsed time betwen jams
  } else {
    jamTime = millis() - startTime;       //check how much time is between jams and store this in jamTime
  }
  if (jamTime < (runConf.minJamTime)) {        //if that is inside unacceptable limits
    jammedCounter++;                         //count this as a jam
    startTime = millis();       //reset the start time
#ifdef DEBUG
    Serial.print("I jammed ");
    Serial.print(jammedCounter);
    Serial.println(" times.");
#endif
  } else {                        //If it has been ages since the last jam
    startTime = millis();
    jammedCounter = 1;                 //start counting again
  }
  lcd.setCursor(0, 0);
  lcd.print("I jammed ");
  lcd.print(jammedCounter);
  lcd.print(" times now  ");
}


void alarm() {
#ifdef DEBUG
  Serial.println("I am jammed");
#endif
  alarmed = true;
  lcd.setCursor(0, 0);
  lcd.print("Alarm: ");
  lcd.print(jammedCounter);
  lcd.print(" jams    ");
}

void checkDirection() {
  /*
      Code assumes a 3 states button with two pins (active high)
      1. Shred
      2. Reverse
      If none is pushed we assume it is off
      It's not possible to push both at the same time (in that case we assume shred forward)
  */
  int shredInput = digitalRead(shredButton);            //check which button is pressed
  int reverseInput =  digitalRead(reverseButton);
  if (shredInput == LOW && reverseInput == LOW) {       //if you are set to stop
    if (working) {
      halt();                                           //don't move
      working = false;
      shredDir = SHRED_ST;
      jamState = JAMMED_NO;
      //      jammedCounter = 0;                              //Should we restart jamming count?
      alarmed = false;
    }
  } else {
    if (!working) {
      working = true;
      lastStart = millis();
    }
    //TODO: check rotation shift and wait before changing
    if (shredInput == HIGH) {                         //if you are set to shred
      if (shredDir != SHRED_FW) {
        shred();                                      //shred
        shredDir = SHRED_FW;
      }
    } else {                                          //if you are set to reverse
      if (shredDir != SHRED_REV) {
        reverse();                                    //turn back
        shredDir = SHRED_REV;
      }
    }
  }
}

void restoreConfig(){
  runConf = {
    D_V0A,
    D_START_SPAN,
    D_MAX_JAMS,
    D_MIN_JAM_TIME,
    E_UNJAM_REVERSE_T,
    0
  };
  runConf.maxCurrent = A_2_AREAD(MAX_CURRENT); //Max current should be calculated after we have loaded config voltage offset for 0A(v0A)
  saveConfig();
}
void readConfig() {
  int address = 0;
  char id[4];
  byte ver;
  EEPROM.get(address, id);
  address += sizeof(id);
  ver = EEPROM[address];
  address++;

  if ((strcmp(id,EEPROM_ID)!=0) || (ver != EEPROM_V)) {
#ifdef DEBUG
    Serial.println("No config found!\n  Restoring to default config");
#endif
    restoreConfig();
  } else {
    EEPROM.get(address, runConf);
#ifdef DEBUG
    Serial.println("Config loaded correctly");
    Serial.print("0A analogRead offset: "); Serial.println(runConf.v0A);
    Serial.print("@ start wait for "); Serial.print(runConf.startSpan); Serial.println("ms before detecting jams");
    Serial.print("Alarm in case of "); Serial.print(runConf.maxJams);
    Serial.print(" jams detected within "); Serial.print(runConf.minJamTime); Serial.println("ms");
    Serial.print("Reverse for "); Serial.print(runConf.unjamReverseT); Serial.println("ms to unjam");
    Serial.print("Detect jam when current over "); Serial.println(AREAD_2_A(runConf.maxCurrent));
#endif
  }
#ifdef DEBUG
  if (ver != EEPROM_V) {
    Serial.println("Invalid config version found");
  }
#endif
}
void saveConfig() {
  // We use EEPROM.put to write to EEPROM to handle structure and as a bonus uses update that only writes if data has changed, improving EEPROM life
  int address = 0;
  char id[4]=EEPROM_ID;
  byte ver = EEPROM_V;
  EEPROM.put(address, id);
  address += sizeof(id);
  EEPROM.put(address, ver);
  address++;
  EEPROM.put(address, runConf);
}

void printBar() {       //displays the drawn current as a bar
  int pBari = map(current, runConf.v0A + 10, runConf.maxCurrent, 0, 17); // turn the current current value into a percentage of the currentcap, considering sensor 0 value
  for (i = 0; i < 17; i++) {
    lcd.setCursor(i, 1);
    if (i > pBari)
      lcd.print(" ");
    else
      lcd.write(byte(0));
  }
}

void printValue() {           //displays the drawn current as a value
  lcd.setCursor(0, 1);
  if (current < 1000)lcd.print(" ");
  lcd.print(current);
  lcd.print(" out of ");
  lcd.print(runConf.maxCurrent);
  lcd.print(" ");
}

void printCurrent() {
  float currentA = AREAD_2_A(current);
  if (currentA < 0)currentA = 0;
  if (millis() < lastCurrentPrint + 250) {
    currentAvg += currentA;
    currentCount++;
    return;
  }
  lastCurrentPrint = millis();
  lcd.setCursor(11, 0);
  if (currentCount == 0)
    lcd.print(currentA);
  else
    lcd.print(currentAvg / currentCount);
  lcd.setCursor(15, 0);
  lcd.print("A");
  currentAvg = 0;
  currentCount = 0;
}

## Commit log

2020-01-07 starterkit - shredder
    [Large sorting trolley.STEP, SHRPRO-V1 1000.01-A Coupling cover.SLDPRT, SHRPRO-V1 1000.01-A Coupling cover.step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]
2020-01-07 added readme
    [Template - Workspace Calculator.xlsx, Urban Miners - Workspace Calculator.xlsx]
2020-01-19 Update Shredder Pro Drawings
    Put it in Sync with the Main download-kit
    [102 RESISTOR PACK.SLDPRT, 15pin_header__.sldprt, 16mhz crystal - measured.SLDPRT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]
